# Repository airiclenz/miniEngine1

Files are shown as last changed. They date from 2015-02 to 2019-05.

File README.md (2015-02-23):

# miniEngine1
An Arduino based single-axis motion-control system for time-lapse photography (the legacy version)

This repository contains all that is needed to build a full miniEngine 1 system. It contains:

	- Software
	- Hardware (PCB CAD files)
	- Documentation
	- Licenses
	
The PCBs and most of the needed parts can be purchased here: http://shop.airiclenz.com  

Notice regarding compilation
----------------------------

The legacy code does not compile with the newest Arduino SDK! Please download the Arduino SDK version 1.0.6 from here: 

http://arduino.cc/en/Main/OldSoftwareReleases

This should compile the code just fine. You will also need to install the RTC library for being able to compile and upload the sketch. Details how to do that can be found in the documentation folder of this repository.

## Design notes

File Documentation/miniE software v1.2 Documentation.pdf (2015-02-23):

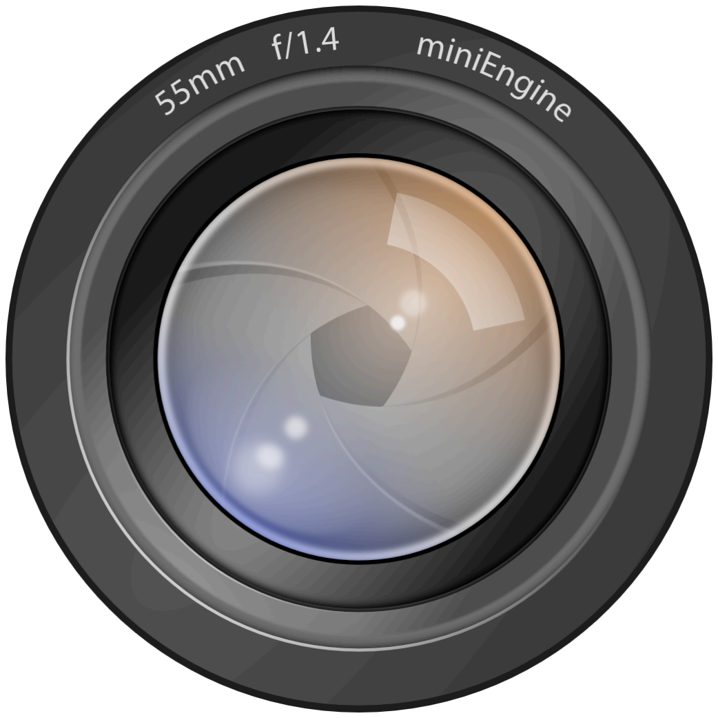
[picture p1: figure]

# miniE

### miniEngine - an open-source motion control system for timelapse photography

# Documentation of version 1.2

## Airic Lenz

### Content

| 1 | Introduction | 1
| 2 | Needed hardware | 1
| 3 | Installation | 3
| 4 | User interface and navigation | 4
| 5 | The Cycle | 5
| 6 | Functionalities | 6
| 6.1 | The main screen | 6
| 6.2 | Camera Functionalities / Settings | 7
| Cycle length | 7
| Focus time | 7
| Exposure time | 7
| Focus-line behaviour | 8
| Max shots | 8
| Post delay | 8
| Test shot | 8
| 6.3 | Motor Functionalities / Settings | 9
| Motor steps | 9
| Motor direction | 9
| Motor post delay | 9
| Move to home | 9
| Set motor home | 9
| Motor sleep | 9
| Max steps | 10
| Motor ramp | 10
| Max speed delay | 10
| Min speed delay | 10
| 6.4 | Programs | 11
| Add program | 11
| Program start time | 11
| Program weekdays | 12
| Program duration | 12
| Move motor home after program | 12
| Program status | 12
| Delete program | 12
| 6.5 | General settings | 13
| Operation mode | 13
Documentation | v1.2

| System time | 13
| Backlight delay | 13
| Backlight power | 13
| Limit switches | 13
| 6.6 | Settings | 14
| Save settings | 14
| Autosave settings | 14
| Reset settings | 14
| 6.7 | Version info | 14
Appendix | 15
Software License | 18
Hardware License | 18

### | 1 | Introduction

miniE is an engine sketch to provide control over a single stepper motor and camera, using an Arduino board and a DFRobot LCD Keypad shield. It is a minimalist design providing all the necessary features to do shoot-move-shoot or continuous timelapse with a built-in user interface. It was developed to provide a slim and easy way to timelapse photography. The first version of miniE was inspired by the OpenMoCo timelapse engine. For more details please have a look at www.airiclenz.com.

### | 2 | Needed hardware

For running the miniEngine you will need an Arduino Uno Board and the DFRobot Display shield for a minimal setup. With these components (and some breadboard magic) you are able to use the system as an intervalometer for your camera. To avoid the open wires and the breadboard I suggest the usage of a Arduino proto-shield for placing the electronics.

For a full setup that uses all capabilities of the current version, you will need the following components:

1x Arduino Uno

1x DFRobot Display Shield

1x RTC module (only needed for timed programs)

1x Stepper motor driver (e.g. EasyDriver)

1x Stepper motor fitting your requirements

1x Dolly system to control

Computer running Windows, Linux, or OSX compatible with the Arduino IDE (≥ 1.0)

Some additional material for wiring up all components (e.g. proto Shield, wires, …)

1x Camera remote cable (u can use a cheap remote for you camera model to get one)

You will also need some electric parts for setting up the required connections to all the external components (like camera, motor driver, ...). Here is a list of all parts needed (for more details have a look at the circuit diagram in the APPENDIX of this document):

CAM | 2.5 mm headphone jack (DigiKey PartNo.: CP1-2503A-ND)
LIMIT-SWITCHES | 2.5 mm headphone jack (DigiKey PartNo.: CP1-2503A-ND)
RTC | Sparkfun RTC MODULE (OPTIONAL)
MOTOR-CONTROL | Terminal screw block 1×3 (pitch 2.54 mm)
MOTOR-ENERGY | Terminal screw block 1×2 (pitch 2.54 mm)
OK1 | 4N35 Optocoupler (DIL-6)
OK2 | 4N35 Optocoupler (DIL-6)
R1 | 470 Ω Resistor (0207/10)
R2 | 470 Ω Resistor (0207/10)
R3 | 20 kΩ Resistor (0207/10)
R4 | 20 kΩ Resistor (0207/10)
R5 | 20 kΩ Resistor (0207/10; OPTIONAL)
S-DY1 | 12V 0.2A diode (e.g. fast zener or schottky diode); This part is OPTIONAL and by default bridged on the miniE shield
S-DY2 | 12V 0.2A diode (e.g. fast zener or schottky diode); This part is OPTIONAL and by default bridged on the miniE shield

If you plan to do timelapse photography from a tripod without any movement of the camera, you will of course not need the movement components like stepper motor, driver board or the dolly system.

### | 3 | Installation

If you don‘t already have installed the Arduino Development Suite, please download it from

http://arduino.cc

and install it. The miniE software can be downloaded from the OpenMoCo SourceForge subVersion repository:

http://openmoco.svn.sourceforge.net/viewvc/openmoco/miniE/trunk/miniE

Now, after you downloaded the project, please unzip (if you downloaded a tarBall) or copy it to any location you want. To successfully compile the miniE code, you need an external library, that is used within miniE. To be able to install the external library, please download it from:

https://github.com/jcw/rtclib

After you downloaded the library, you need to install it. To do so, unzip it. It should be in a folder of its own. Open the Arduino folder. This folder should be placed in your user accounts documents folder (You can check the path in the Arduino settings). On a Mac this folder usually can be found here:

/Users/USERNAME/Documents/Arduino

On a Windows system this folder should be placed here:

Drive:\Users\USERNAME\My Documents\Arduino

If there is already a folder there called libraries, place the RTClib folder in there. If not, create a folder called libraries in the Arduino folder, and drop the RTClib folder in there. Then re-start the Arduino programming environment.

Open the project by double clicking the main project file miniE.ino (all needed files will be loaded automatically then). For uploading the software to your Arduino board, connect your Arduino board (for details about connecting the Arduino, please check the Arduino website and the Arduino documentation) to your computer. Now press the upload button:

After the code was uploaded successfully, your Arduino board is ready for doing timelapse photography for you.

If you don‘t see anything on your screen, please adjust the LCD contrast.

### | 4 | User interface and navigation

The miniE user interface is based on a 2x16 char LCD display and 5 buttons. The full system control is available through this interface. Due to the limited space, available on such a LCD display, the full amount of data and settings is spread over different single setting screens which are available by navigating through a menu tree.

The navigation is based on the general principle that you move sideways through the user interface. A RIGHT key press brings you deeper into the menu structure while a LEFT key press brings you back up. The UP and DOWN keys are used for moving up and down on a menu- or information screen and for changing settings (toggle, increment, decrement). The complete menu tree can be found in Appendix 1 at the end of this document.

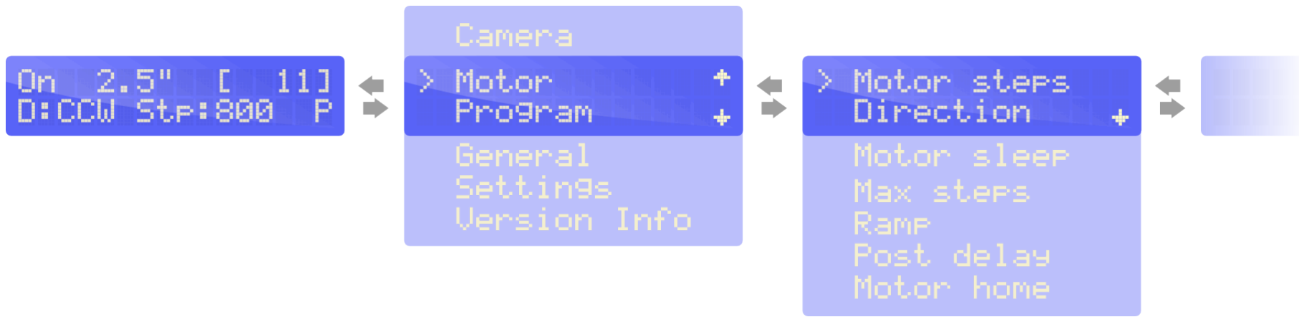
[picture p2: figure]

The navigation principle

### | 5 | The Cycle

The way miniE works can be described as a cycle. Please keep in mind that the total cycle length, you can define, is not a limiting factor. If "Focus time", "Exposure time", "Exposure post delay", the time the motor needs for the movement and the "Motor post delay" are in total longer than the cycle, all these steps will be performed fully in any case. If this happens, the "real“ cycle length is longer than the time you defined for it and equals the sum of all cycle steps.

The picture below shows the ideal situation where all the single steps take in total less time than the defined cycle length.

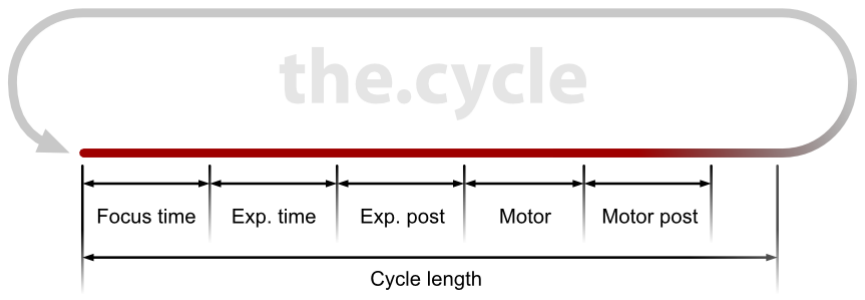
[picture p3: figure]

The cycle of miniE

### | 6 | Functionalities

| 6.1 | The main screen

The main screen is the control central of the miniE system. Here you can start and stop the engine, follow the process and view the most important settings and values. You start and stop the program by pressing the SELECT key.

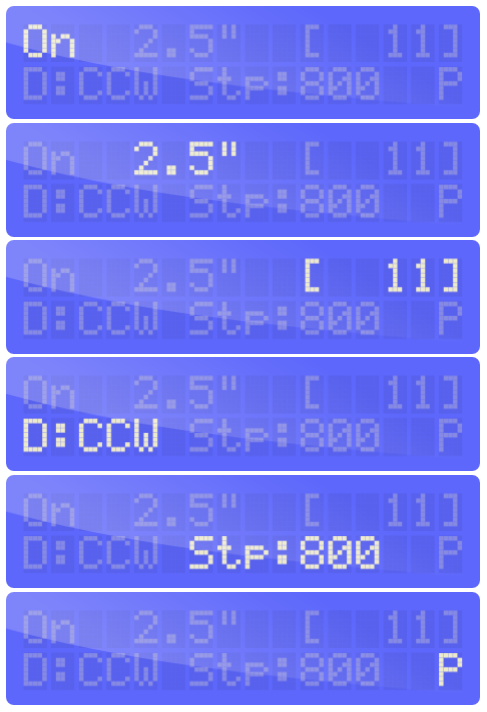
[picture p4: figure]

Status of the engine. This shows if the engine is running or stopped. You can start / stop it by pressing the SELECT key or through a program

Length of the full cycle. You can change this value under [Camera] - [Cycle length]

Number of shots taken since the engine start. This value will be reset every time the engine re-starts

Direction of the motor. CW = clockwise; CCW = counter/anti-clockwise; This can be changed under [Motor] - [Direction]

The number of steps to do during one cycle. This value can be changed under [Motor] -[Motor steps]

Program status. You can only see something here if at least one future program is programmed. If the engine is stopped, you see a static „P“. If you started the engine manually, you will see a blinking „!“ because you possibly prevent a timed program from running. If a timed program is running you will see a blinking „P“

| 6.2 | Camera Functionalities / Settings

| Cycle length

The cycle length defines the length of the main loop of the engine. A cycle length of 5 seconds means that the engine will take a photo every 5 seconds. After that all other cycle tasks, like motor movement, will be performed. After that the engine will wait until the 5 seconds are over (counted from the start of the cycle) and start a new cycle then.

| Focus time

The focus time is the first task during a cycle. It will trigger the focus line of the camera for the amount of milliseconds you defined. This can be used for focussing or to wake up the camera in very long cycles. If you set the focus time to zero, this task will not be performed.

| Exposure time

The exposure time is executed directly after focussing. It will trigger the exposure line of the camera for the amount of milliseconds you defined. This is actually triggering the shutter and doing the shot. You can use this to trigger your camera to do a shot in manual mode. In this case you have to set up your camera with your preferred manual settings.

For triggering the shutter, a minimal exposure time of about 40 milliseconds (1/25) is needed. This value changes from camera brand to camera brand.

If you want to do HDR shoots, you have to set up you camera to do all needed shots after one trigger signal. Another solution would be to expose as long as your camera needs to doo all HDR shots (set the camera drive to multi shot mode for this).

| Focus-line behaviour

This is setting the behaviour of the focus line during the exposure. You can choose between „high with shutter“ and „low with shutter“. This option is needed due to the fact that different camera brands need different signal combinations to accept the shutter signal.

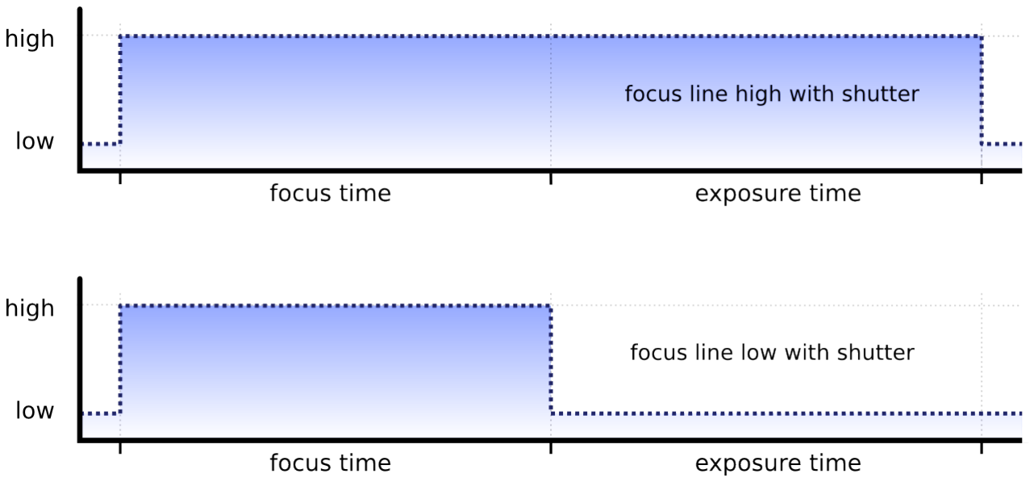
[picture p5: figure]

Focus line behaviour

| Max shots

This is defining a stop limit for the engine. After reaching this amount of shots, the engine will be stopped automatically. A value of „0“ means that there is no limit.

| Post delay

The post delay is a delay time after the exposure time is over. This can be used to ensure the camera has enough time to finnish the exposure before the motor starts to move.

| Test shot

Here you can check if your camera is connected properly and the settings are OK for your specific camera brand. This will do one single exposure with the duration of 1/10th of a second (100 milliseconds).

| 6.3 | Motor Functionalities / Settings

| Motor steps

This setting is for defining the amount of steps to do during your motor phase of the cycle. 1,600 steps are exactly one revelation with most of the stepper motors.

| Motor direction

Here you can set the direction of you motor. You can choose between clockwise and counter-clockwise.

| Motor post delay

This delay is usually used to let the dolly settle down after motor movement to avoid vibrations.

| Motor home menu

This menu contains all settings and functionalities for controlling the motor home behaviour. The motor home position is a free choosable position of the motor. The engine counts every step away from this position while the engine is running (started manually or by a program). You can move the motor back to its home position manually or automatically after a timed program finished.

The motor home position is cleared when miniE is powered up. This means that your motor always starts from home after miniE was powered up.

| Move to home

With this functionality you can move the motor back to its home position manually.

| Set motor home

This sets the current position of the motor as home position.

| Motor sleep

Motor sleep defines the behaviour of the driver board when the motor is not moved. This setting is only valid for the time when the engine is running. While the engine is stopped, the motor is always in sleep mode.

If your motor is in sleep mode between the movements, its energy consumption is drastically reduced.

You can turn sleep mode off to keep the motor powered as long as the engine is running. This is useful if you want to avoid any movements of your dolly during the run.

| Max steps

This is defining a stop limit for the engine. After reaching this amount of steps, the engine will be stopped automatically. A value of „0“ means that there is no limit.

| Motor ramp

This value is defining the amount of steps your motor will accelerate and decelerate through a motor movement phase.

If you defined a value of 200 steps for ramping and you are doing 1000 steps each cycle, your motor phase looks like this:

- 200 steps acceleration
- 600 steps max speed
- 200 steps deceleration

The motor ramping softly shaped for smooth movements.

| Max speed delay

This value defines the time between every motor step at maximum speed. The shorter the delay is, the faster your motor is running.

| Min speed delay

This value defines the time between every motor step at minimum speed (At the very beginning and at the very end of every motor phase). The longer the delay is, the slower your motor is running.

| 6.4 | Programs

Programs are used to start the engine automatically at a defined time and date. Programs only work if you have a Real-Time-Clock connected to your Arduino. You can define two types of programs:

- single date program - is only started once
- repeating weekday program - is started at the defined weekdays (e.g. every Monday)

You can define 30 programs. A programs is not started while you are editing it!

In the program list

In the graphic obove you can see the two different program types with their corresponding representation in the program list (24h time format):

- 10. Nov 0900 - Single date program - this program will only be started once (at the 10th November at 09:00 o‘clock in the morning, the year is not displayed in the program list)
- M_W_F_S 1700 - Repeating weekday program - this program is started every Monday, Wednesday, Friday and Sunday at 17:00 o‘clock. A program becomes automatically a repeating weekday program if at least one day of the week is activated for the program (see „Program weekdays“)

| Add program

You can add a new program with this functionality. After you added a program, you are automatically editing it.

| Program start time

You can edit the program start time here. This is the time the engine will started automatically. If the program is a single date program, you will be able to define a date (this is not the case if you are editing a repeating weekday program).

| Program weekdays

Here you can set weekdays at which you want the program to be started. If you deactivate all weekdays, the program becomes a single date program and will only be started once.

| Program duration

This value defines the duration in minutes the engine will be active after it was started by the program.

| Move motor home after program

If enabled, the motor will automatically move back to its home position (see Motor home for more information) after the program was stopped. The motor will be moved back on any event that stops the program (regular end, limit switch, manually stopped by the user).

| Program status

If enabled, the program is active and will be considerated by the internal timer. If you disable a program, it has the same effect as if it were not existing.

| Delete program

Here you can delete the program you are currently editing.

| 6.5 | General settings

| Operation mode

The operation mode is defining the basic way the miniEngine will work. You can choose between two different modes:

- shoot-move-shoot mode - the shoot-move-shoot mode is doing all steps of the cycle sequentially. This means the camera is triggered, then the motor moves, and then the cycle begins again.
- continuous mode - in this mode the motor is moving continually (The amount of defined steps per cycle). The camera is triggered while the motor is moving.

| System time

You can set the system time here. This functionality is only available if you have a Real-Time-Clock connected to your system.

| Backlight delay

This value defines the time in seconds the system is waiting after the last user action, until shutting off the LCD-backlight.

| Backlight power

Here you can set the brightness of your LCD-backlight.

| Limit switches

You can turn the limit-switches on or off. If you disable your limit switches, a triggered limit-switch will not stop the running engine.

This functionality is included because a not installed limit switch can cause unwanted limit switch events (the Arduino ports, used for the limit switches, are very sensitive and need to be pulled down to ground through a pull-down resistor with a value between 1kΩ and 50kΩ). If there is no pull-down resistor, it is better to turn off the limit switches.

| 6.6 | Settings

| Save settings

This functionality is saving all your defined values and settings to the internal EEPROM of the Arduino board. After powering the system all settings and values are automatically loaded from the EEPROM.

| Autosave settings

You can save all settings and values automatically. If you enable this functionality the the settings are automatically saved after you changed any setting or value and left the corresponding setting / value screen.

| Reset settings

This functionality is resetting all settings and values to the default values. It is also deleting all defined programs.

| 6.7 | Version info

Some information about the current installed version of miniEngine.

### Appendix

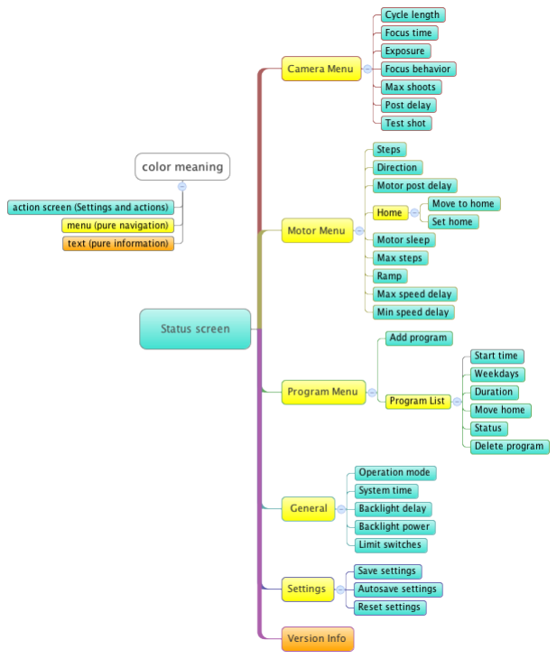
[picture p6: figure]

APPENDIX 1 - The menu tree

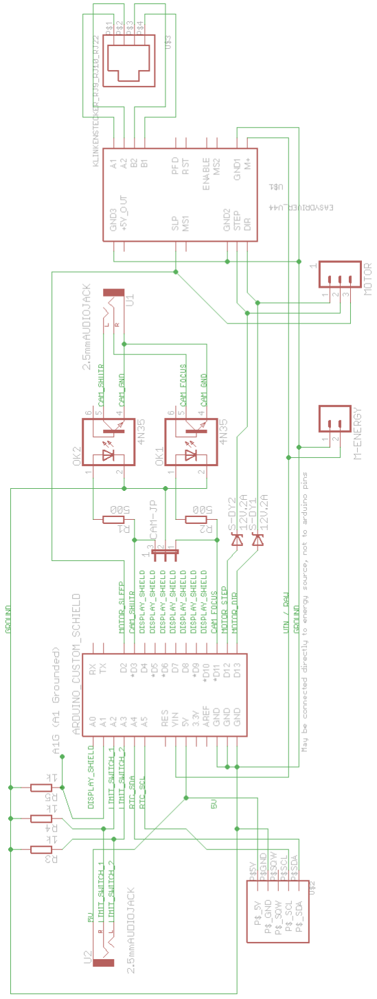
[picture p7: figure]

APPENDIX 2 - Circuit diagram

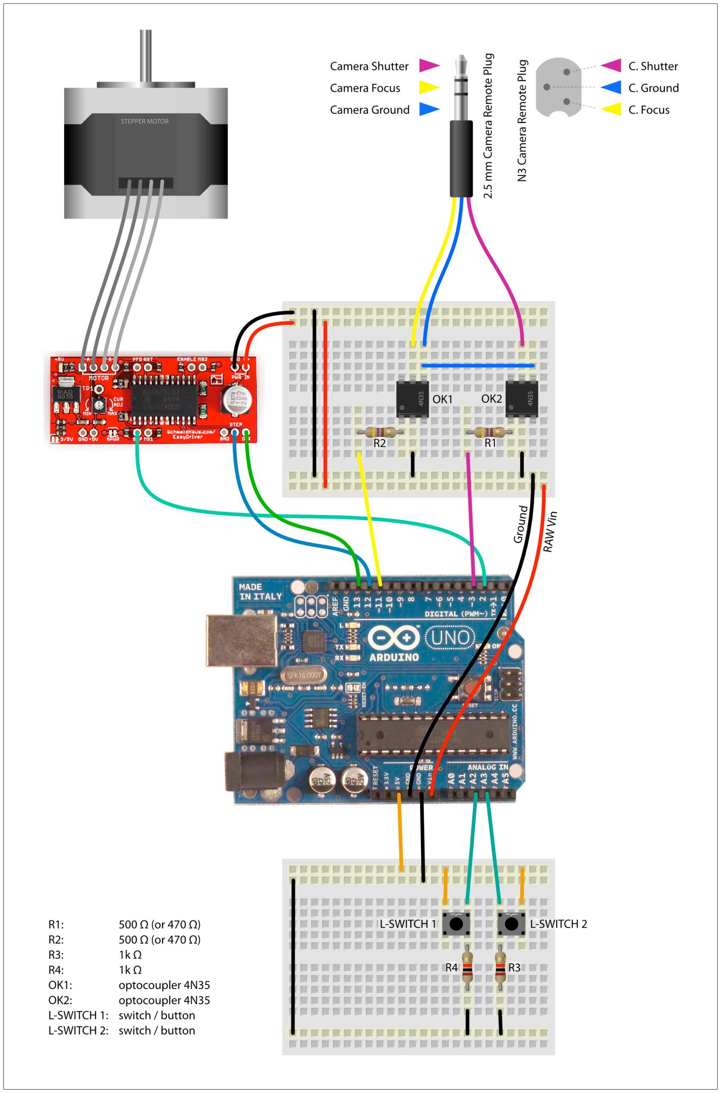
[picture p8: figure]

APPENDIX 3 - Arduino breadboard circuit

### Software License

The miniEngine software is free software: you can redistribute it and/or modify it under the terms of the GNU General Public License as published by the Free Software Foundation, either version 3 of the License, or (at your option) any later version.

The miniEngine software and all belonging material is distributed in the hope that it will be useful, but WITHOUT ANY WARRANTY; without even the implied warranty of MERCHANTABILITY or FITNESS FOR A PARTICULAR PURPOSE. See the GNU General Public License for more details.

You should have received a copy of the GNU General Public License along with this program. If not, see http://www.gnu.org/licenses/.

### Hardware License

All hardware designs and schematics provides along with the miniE software are free. You can redistribute it and/or modify it under the terms of the CERN Open Hardware Licence 1.1, or (at your option) any later version.

The hardware documentation and hardware files are distributed in the hope that they will be useful, but WITHOUT ANY WARRANTY; without even the implied warranty of MERCHANTABILITY or FITNESS FOR A PARTICULAR PURPOSE. See the CERN Open Hardware Licence for more details.

You should have received a copy of the CERN Open Hardware Licence along with these files. If not, see http://www.ohwr.org/projects/cernohl/wiki/.

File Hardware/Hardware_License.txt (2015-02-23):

CERN OPEN HARDWARE LICENCE v1.1

Preamble

Through this CERN Open Hardware Licence ("CERN OHL") version 1.1, the
Organization wishes to disseminate its hardware designs (as published
on http://www.ohwr.org/) as widely as possible, and generally to
foster collaboration among public research hardware designers. The
CERN OHL is copyright of CERN. Anyone is welcome to use the CERN OHL,
in unmodified form only, for the distribution of his own Open Hardware
designs. Any other right is reserved.  

1. Definitions

In this Licence, the following terms have the following meanings:

“Licence” means this CERN OHL.  

“Documentation” means schematic diagrams, designs, circuit or circuit
board layouts, mechanical drawings, flow charts and descriptive text,
and other explanatory material that is explicitly stated as being made
available under the conditions of this Licence. The Documentation may
be in any medium, including but not limited to computer files and
representations on paper, film, or any other media.  

“Product” means either an entire, or any part of a, device built using
the Documentation or the modified Documentation.  

“Licensee” means any natural or legal person exercising rights under
this Licence.  

“Licensor” means any natural or legal person that creates or modifies
Documentation and subsequently communicates to the public and/ or
distributes the resulting Documentation under the terms and conditions
of this Licence.  

A Licensee may at the same time be a Licensor, and vice versa.

2. Applicability

2.1 This Licence governs the use, copying, modification, communication
to the public and distribution of the Documentation, and the
manufacture and distribution of Products. By exercising any right
granted under this Licence, the Licensee irrevocably accepts these
terms and conditions.  

2.2 This Licence is granted by the Licensor directly to the Licensee,
and shall apply worldwide and without limitation in time. The Licensee
may assign his licence rights or grant sub-licences.  

2.3 This Licence does not apply to software, firmware, or code loaded
into programmable devices which may be used in conjunction with the
Documentation, the modified Documentation or with Products. The use of
such software, firmware, or code is subject to the applicable licence
terms and conditions.  

3. Copying, modification, communication to the public and distribution
of the Documentation

3.1 The Licensee shall keep intact all copyright and trademarks
notices and all notices that refer to this Licence and to the
disclaimer of warranties that is included in the Documentation. He
shall include a copy thereof in every copy of the Documentation or, as
the case may be, modified Documentation, that he communicates to the
public or distributes.

3.2 The Licensee may use, copy, communicate to the public and
distribute verbatim copies of the Documentation, in any medium,
subject to the requirements specified in section 3.1.

3.3 The Licensee may modify the Documentation or any portion
thereof. The Licensee may communicate to the public and distribute the
modified Documentation (thereby in addition to being a Licensee also
becoming a Licensor), always provided that he shall: 
a. comply with section 3.1;
b. cause the modified Documentation to carry prominent notices stating
that the Licensee has modified the Documentation, with the date and
details of the modifications;
c. license the modified Documentation under the terms and conditions
of this Licence or, where applicable, a later version of this Licence
as may be issued by CERN; and
d. send a copy of the modified Documentation to all Licensors that
contributed to the parts of the Documentation that were modified, as
well as to any other Licensor who has requested to receive a copy of
the modified Documentation and has provided a means of contact with
the Documentation.

3.4 The Licence includes a licence to those patents or registered
designs that are held by the Licensor, to the extent necessary to make
use of the rights granted under this Licence. The scope of this
section 3.4 shall be strictly limited to the parts of the
Documentation or modified Documentation created by the Licensor.

4. Manufacture and distribution of Products

4.1 The Licensee may manufacture or distribute Products always
provided that the Licensee distributes to each recipient of such
Products a copy of the Documentation or modified Documentation, as
applicable, and complies with section 3.

4.2 The Licensee is invited to inform in writing any Licensor who has
indicated its wish to receive this information about the type,
quantity and dates of production of Products the Licensee has (had)
manufactured.

5. Warranty and liability

5.1 DISCLAIMER – The Documentation and any modified Documentation are
provided "as is" and any express or implied warranties, including, but
not limited to, implied warranties of merchantability, of satisfactory
quality, and fitness for a particular purpose or use are disclaimed in
respect of the Documentation, the modified Documentation or any
Product. The Licensor makes no representation that the Documentation,
modified Documentation, or any Product, does or will not infringe any
patent, copyright, trade secret or other proprietary right. The entire
risk as to the use, quality, and performance of a Product shall be
with the Licensee and not the Licensor. This disclaimer of warranty is
an essential part of this Licence and a condition for the grant of any
rights granted under this Licence. The Licensee warrants that it does
not act in a consumer capacity.

5.2 LIMITATION OF LIABILITY – The Licensor shall have no liability for
direct, indirect, special, incidental, consequential, exemplary,
punitive or other damages of any character including, without
limitation, procurement of substitute goods or services, loss of use,
data or profits, or business interruption, however caused and on any
theory of contract, warranty, tort (including negligence), product
liability or otherwise, arising in any way in relation to the
Documentation, modified Documentation and/or the use, manufacture or
distribution of a Product, even if advised of the possibility of such
damages, and the Licensee shall hold the Licensor(s) free and harmless
from any liability, costs, damages, fees and expenses, including
claims by third parties, in relation to such use.

6. General

6.1 The rights granted under this Licence do not imply or represent
any transfer or assignment of intellectual property rights to the
Licensee.

6.2 The Licensee shall not use or make reference to any of the names,
acronyms, images or logos under which the Licensor is known, save in
so far as required to comply with section 3. Any such permitted use or
reference shall be factual and shall in no event suggest any kind of
endorsement by the Licensor or its personnel of the modified
Documentation or any Product, or any kind of implication by the
Licensor or its personnel in the preparation of the modified
Documentation or Product.

6.3 CERN may publish updated versions of this Licence which retain the
same general provisions as this version, but differ in detail so far
this is required and reasonable. New versions will be published with a
unique version number.

6.4 This Licence shall terminate with immediate effect, upon written
notice and without involvement of a court if the Licensee fails to
comply with any of its terms and conditions, or if the Licensee
initiates legal action against Licensor in relation to this
Licence. Section 5 shall continue to apply.

6.5 Except as may be otherwise agreed with the Intergovernmental
Organization, any dispute with respect to this Licence involving an
Intergovernmental Organization shall, by virtue of the latter's
Intergovernmental status, be settled by international arbitration. The
arbitration proceedings shall be held at the place where the
Intergovernmental Organization has its seat. The arbitral award shall
be final and binding upon the parties, who hereby expressly agree to
renounce any form of appeal or revision.

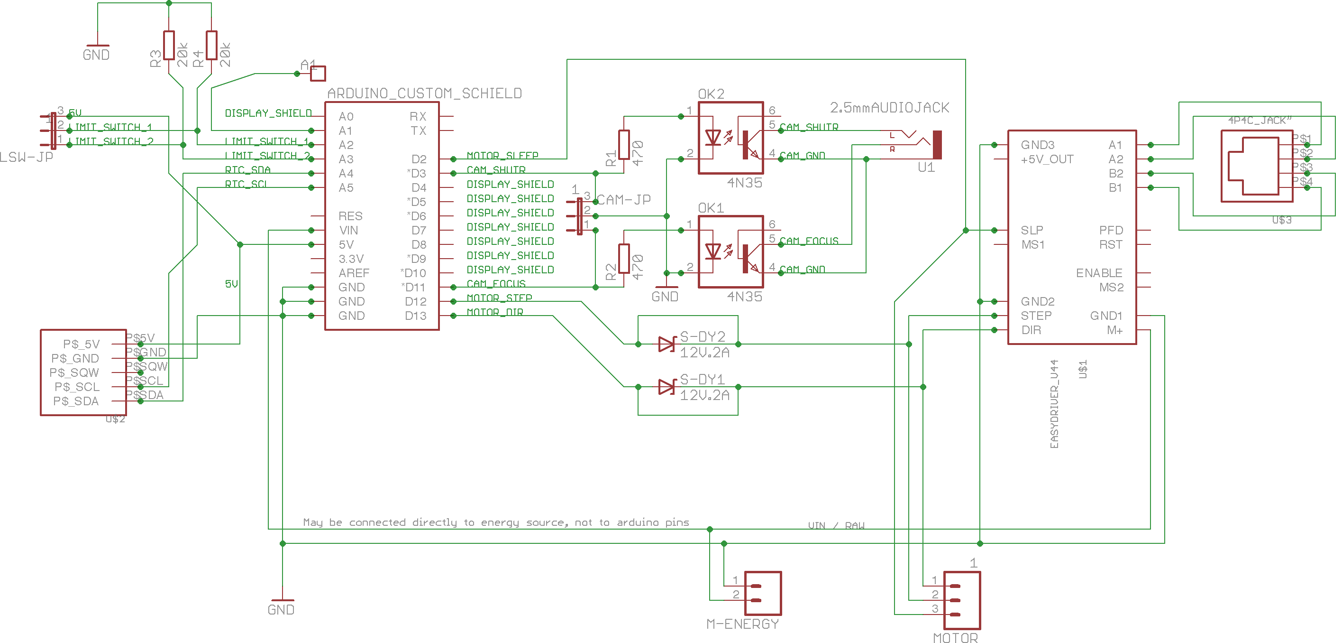
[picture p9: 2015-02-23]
Hardware/miniE_arduino_shield_v1-3.png

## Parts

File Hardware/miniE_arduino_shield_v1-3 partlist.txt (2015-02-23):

miniE shield - version 1.2 - part list
2012 by Airic Lenz

===================================================================================
PART                   VALUE / TYPE           PACKAGE                 
===================================================================================
CAM                    2.5MM HEADPHONE JACK   DigiKey PartNo.: CP1-2503A-ND                   
LSW	                   TERMINAL               Terminal-1x3 (2.54mm pitch)       
OK1                    4N35                   DIL06 OPTOCOUPLER                     
OK2                    4N35                   DIL06 OPTOCOUPLER                     
R1                     470~510 Ohm            RESISTOR 0207/10                     
R2                     470~510 Ohm            RESISTOR 0207/10                    
R3                     10k~20k Ohm            RESISTOR 0207/10                     
R4                     10k~20k Ohm            RESISTOR 0207/10                     
EASYDRIVER v4.4        -                      EASYDRIVER V4.4              
MOTOR                  4C4C PHONE JACK        DigiKey PartNo.: AE10381-ND	

OPTIONAL:
===================================================================================
PART                   VALUE / TYPE           PACKAGE                 
===================================================================================

S-DY1                  12V 0.2A               DIODE schottky/zener (bridged by default)            
S-DY2                  12V 0.2A               DIODE schottky/zener (bridged by default)        

If no EasyDriver should be used:
-----------------------------------------------------------------------------------
( MOTOR ) CONTROL      TERMINAL               Terminal-1x3 (2.54mm pitch)		
( MOTOR ) POWER        TERMINAL               Terminal-1x2 (2.54mm pitch)                        

If the camera should be triggered via infrared-LED:
-----------------------------------------------------------------------------------
IR                     TERMINAL               Terminal-1X3 (2.54mm pitch)

If you want to use scheduled programs:
(see http://www.sparkfun.com/products/99 for the used module)
-----------------------------------------------------------------------------------
RTC MODULE             DS1307                 SPARKFUN RTC MODULE (BOB-00099)

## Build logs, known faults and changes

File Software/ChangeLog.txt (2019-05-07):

===============================================================================
   C H A N G E   L O G  -   m i n i E n g i n e
===============================================================================

=====  v1.2a  ===  2019-05-07  ================================================

-	Adaption to the latest Arduinio SDK version

=====  v1.2  ===  2015-02-23  =================================================

-	bug fixes
-	Improved the motor min-speed code

=====  v1.1  ===  2012-05-06  =================================================

-	added 2 new ramping types -> now 3 motor ramping types
	(which is bes used can be changed in the code)
	main file line 133)
	> ARCTAN (new default - much smoother)
	> LINEAR
	> SINUS
- 	added limit switch checks to the motor phases (every 150ms)
-	added check for SELECT key to the motor phases (motor phases are no longer
	blocking)

=====  v1.00 ===  2012-03-22  =================================================

-	fixed a bug with minimum values (backlight time = zero problem)

=====  v0.12 ===  2012-02-13  =================================================

-	fixed a bug in the menu navigation
-	fixed a bug that if on system-time-screen the time is now updated
	automatically
- 	changed the ramping algorithm - ramping is now much smoother

=====  v0.11 ===  2012-02-12  =================================================

-	fixed a bug in the menu navigation - in some cases one were
	not able to move away from the main status screen
-	optimized key values (analogue values) for more precise key readings

=====  v0.10 ===  2012-01-06  =================================================

-	Upgraded MiniE to be compatible with Arduino 1.0
-	Fixed link to new Arduino 1.0 jeelabs RTC Lib
- 	Extended limit switch slightly where it will reverse the motor and
  	run one load of steps in the reverse direction to stop limit switch
- 	Lowered the detection for the limit switches (from 1023 to more than 1000)
- 	Reduced strings used to lower sketch size, Arduino 1.0 ended up blowing
  	the size out by 200bytes, pushign it over the UNO & ATMega328p limit
- 	Created new function to fill out menus to reduce code size (Could still be
  	extended to include other menus)

=====  v0.9 ===  2011-10-09  ==================================================

-	Added documentation for v0.9

=====  v0.9 ===  2011-09-21  ==================================================

-	Added units to the different setting-screens
-	Menu positions are now saved. When you go back in a menu, the focus is
	placed on the item you were at before
-	Added two 1k resistors to the two limit switch pins to generate clear
	signals (see circuit diagram for more details) and avoid unwanted
	limit-switch-triggerings
-	Added the possibility to enable/disable limit switches in the software
-	Added the possibility to set min and max motor speeds (step delays:
	big delay = slow; short delay = fast)
-  	Fixed the issue that focus line did not close after program end and
	during motor home movement

=====  v0.8.1 ===  2011-09-14  ================================================

-	Minor bugfix (system time editor)

=====  v0.8 ===  2011-09-13  ==================================================

-	The "P" for existing programs on the main screen is now only
	displayed if there are programs that will become active in the future.
	(smart "P")
-	Added a motor post delay
-	The system time is now editable
-	Updated copyright information
-	Fixed an issue that led the engine to heavy lagging while starting and
	stopping the continuous mode
-	Fixed a bug that crashed the engine in continuous mode after a limit
	switch event

=====  v0.7 ===  2011-09-07  ==================================================

-	Continuous mode is now 100% precise
-	Cycle length can now be adjusted in 0.5 second steps
-	Fixed a bug in motor-home counting
-	Fixed crashed motor ramping from version 0.6

=====  v0.6 ===  2011-09-06  ==================================================

-	Extensive optimisations of the UI code regarding RAM usage
-	Added RTC functionality
-	Added the possibility to create up to 30 programs
	(single date programs, repeating weekday programs)
-	Programs can be saved / autosaved together with the settings
-	Deleted "load settings" (useless because settings are automatically
	loaded during boot)
-	Added "reset settings" functionality. This resets all settings to
	factory default and deletes all programs.
-	Added message system to allow pop-up screen messages
-	Bugfix of a limit switch error that allowed one more cycle with triggered
	limit switch when restarting the engine
-	Minor bugfixes, code- and usability optimisations

=====  v0.5 ===  2011-08-29  ==================================================

-	Fixed the motor pin error (exchanged pin 12 & 13 to fit the circuit
	diagram)
-	added EEPROM functionality for saving and restoring all settings
-	Optimized menu code (in preparation for the RTC-program feature coming)
-	Added max shot limit
-	Added max motor step limit (counting from motor home)
-	Added backlight control features (duration and brightness)
- 	Minor bugfixes
-	Moved limit switch pins to analog pins 3 and 4

=====  v0.4 ===  2011-08-26  ==================================================

-	Minor code optimizations
-	Optimized long-key-press speed up
-	Added limiting switches check to analog pins 4 and 5.
	When connected to 5V the program stopps
-	Added the motor-home counter for the continuous mode - motor home now
	works in continuous mode too
-	The number of shoots done now stays displayed after the program stopped
-	Fixed an error in home counting in shoot-move-shoot mode

=====  v0.3  ===  2011-08-19  ==================================================

-	Changed the default value for focus line behavior to low with shutter
-	Implemented motor sleep functionality (new menu entry in "Motor")
	(motor is always in sleep while program stopped)
-	Added resistors in front of the optocouplers and updated the circuit
	diagram

=====  v0.2  ===  2011-08-18  ==================================================

-	Camera focus was implemented and is executed before the
	camera exposes (new menu entry under "Camera")
-	"Focus behavior" was implemented. This is setting the behavior
	of the focus line while exposing (high or low) (new menu
	entry in "Camera")
-	Added a little documentation describing "the cycle" of miniE

=====  v0.1  ===  2011-07-06  ==================================================

First version with the following features:

-	Arduino (ATMega) based Motion Control system
	for use with the DFRobot LCD Shield
-	System control is fully implemented as a 5 button -
	16x2 char GUI
-	Supports 1 stepper motor
-	Supports 1 camera
-	Shoot-move-shoot mode
-	continuous mode (needs to be improved)
-	Sinus shaped motor ramping (up to 32 mio steps)
-	Auto backlight-off after 15 seconds
	(still hard wired in the code)
- 	Motor home (for shoot-move-shoot mode)
-	Exposure post delay

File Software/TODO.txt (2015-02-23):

TODO

[ ] change limit switch behaviour from default low to default high if possible

[ ] Implement better limit-switch-event-protocol:
		1. Limit switch detected
		2. Pause for a moment (configurable?)
		3. Reverse at say 1/2 the forward speed (or the minimum speed) until the limit 
		   switch is released (i.e JUST far enough for the limit switch not to 
		   be operated). 

[ ] add #defines which are used to set the drivers specific motor awake or asleep states
	(e.g. sleep = high; awake = low)
	
[ ] add manual clear / auto clear behavior (of the shots taken)

[ ] it would be nice to use max steps and the cycle time to show a 
	calculation of the time to traverse the entire rail.	
	
[ ]	Jog function

[ ]	Add help screens "behind" the action screens describing
	the related function (only if there is flash memory left)
  		
[ ] Tidy up other menu LCD creation steps.

[ ] Move to end (till limit switch).

[ ] Fit IR trigger code in

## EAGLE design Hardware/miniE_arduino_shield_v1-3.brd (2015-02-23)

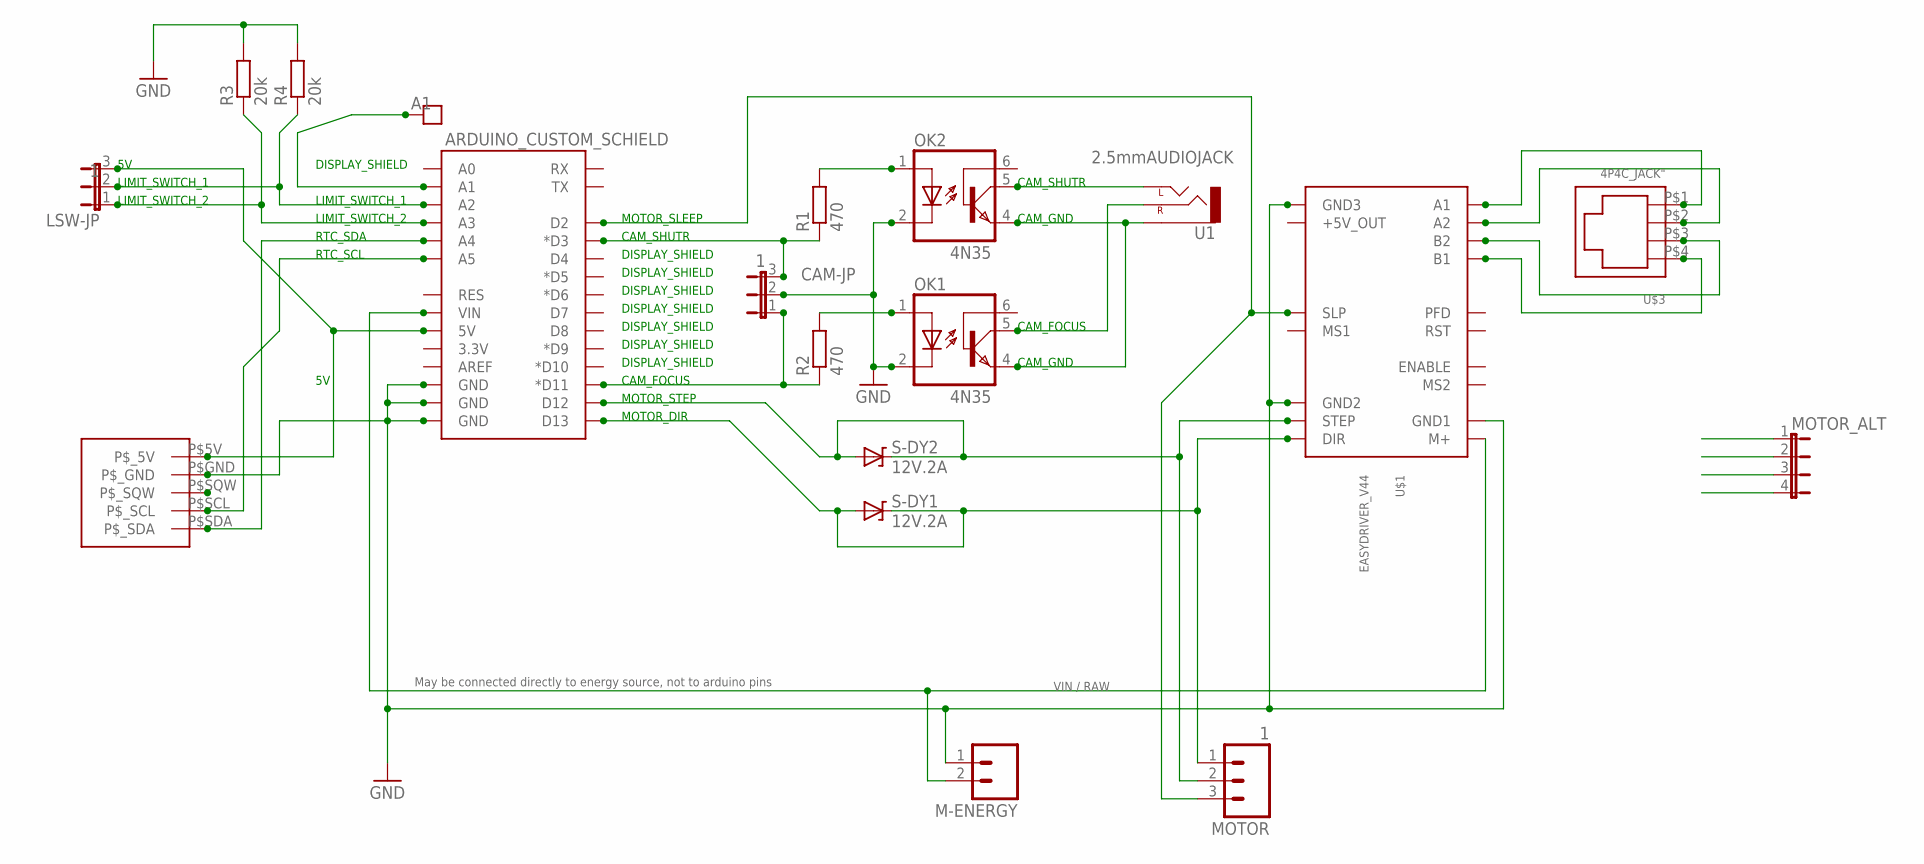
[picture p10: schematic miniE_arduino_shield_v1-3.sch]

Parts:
ARDUINO_CUSTOM_SCHIELD: ARDUINO_SHIELDNOLABELS; DUEMILANOVE_SHIELD_NOLABELS
CAM-JP: 1; JP2
LSW-JP: 1; JP2
M-ENERGY: MOLEX_02; 1X02
MOTOR: 1; 1X03
MOTOR_ALT: JP4E; JP4
OK1, OK2: 4N35; DIL06
R1, R2: 470; 0207/10
R3, R4: 20k; 0207/10
S-DY1, S-DY2: 12V.2A; DIODE-ZENER
U1: 2.5mmAUDIOJACK; STEREOJACK2.5MM_STEREOJACK2.5MM
U$1: EASYDRIVER_V44
U$2: SPARKFUN_RTC_MODULE-OPTIONAL; SPARKFUN_RTC_MODULE_OPTIONAL
U$3: 4P4C_JACK"; 4P4C_JACK-ASS-2004-3-4-LP-N-R
U$4: JUMPER_1X1

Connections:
+5V: ARDUINO_CUSTOM_SCHIELD.5V, LSW-JP.3, U$2.P$5V (P$_5V)
A1: MOTOR_ALT.1, U$1.A1, U$3.P$1
A2: MOTOR_ALT.2, U$1.A2, U$3.P$2
B1: MOTOR_ALT.4, U$1.B1, U$3.P$4
B2: MOTOR_ALT.3, U$1.B2, U$3.P$3
CAM_FOCUS: OK1.5 (COL), U1.RING1 (RIGHT), U1.RING2 (RIGHT)
CAM_GND: OK1.4 (EMI), OK2.4 (EMI), U1.SLEEVE
CAM_SHUTTER: OK2.5 (COL), U1.TIP (LEFT)
GND: ARDUINO_CUSTOM_SCHIELD.GND@0 (GND), ARDUINO_CUSTOM_SCHIELD.GND@1 (GND), ARDUINO_CUSTOM_SCHIELD.GND@2 (GND), CAM-JP.2, M-ENERGY.1, OK1.2 (C), OK2.2 (C), R3.2, R4.2, U$1.GND1, U$1.GND2, U$1.GND3, U$2.P$GND (P$_GND)
unnamed: ARDUINO_CUSTOM_SCHIELD.D12, MOTOR.2, S-DY2.P$1 (C), S-DY2.P$2 (A), U$1.STEP
unnamed: ARDUINO_CUSTOM_SCHIELD.D11 (*D11), CAM-JP.1, R2.1
unnamed: ARDUINO_CUSTOM_SCHIELD.D3 (*D3), CAM-JP.3, R1.1
unnamed: ARDUINO_CUSTOM_SCHIELD.D13, MOTOR.1, S-DY1.P$1 (C), S-DY1.P$2 (A), U$1.DIR
unnamed: ARDUINO_CUSTOM_SCHIELD.D2, MOTOR.3, U$1.SLEEP (SLP)
unnamed: OK2.1 (A), R1.2
unnamed: OK1.1 (A), R2.2
unnamed: ARDUINO_CUSTOM_SCHIELD.A2, LSW-JP.2, R4.1
unnamed: ARDUINO_CUSTOM_SCHIELD.A3, LSW-JP.1, R3.1
unnamed: ARDUINO_CUSTOM_SCHIELD.A4, U$2.P$SDA (P$_SDA)
unnamed: ARDUINO_CUSTOM_SCHIELD.A5, U$2.P$SCL (P$_SCL)
unnamed: ARDUINO_CUSTOM_SCHIELD.A1, U$4.P$1
VIN: ARDUINO_CUSTOM_SCHIELD.VIN, M-ENERGY.2, U$1.M+

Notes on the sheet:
CAM_FOCUS
CAM_GND
CAM_SHUTR
DISPLAY_SHIELD
MOTOR_SLEEP
MOTOR_STEP
MOTOR_DIR
LIMIT_SWITCH_1
LIMIT_SWITCH_2
RTC_SDA
RTC_SCL
VIN / RAW
May be connected directly to energy source, not to arduino pins

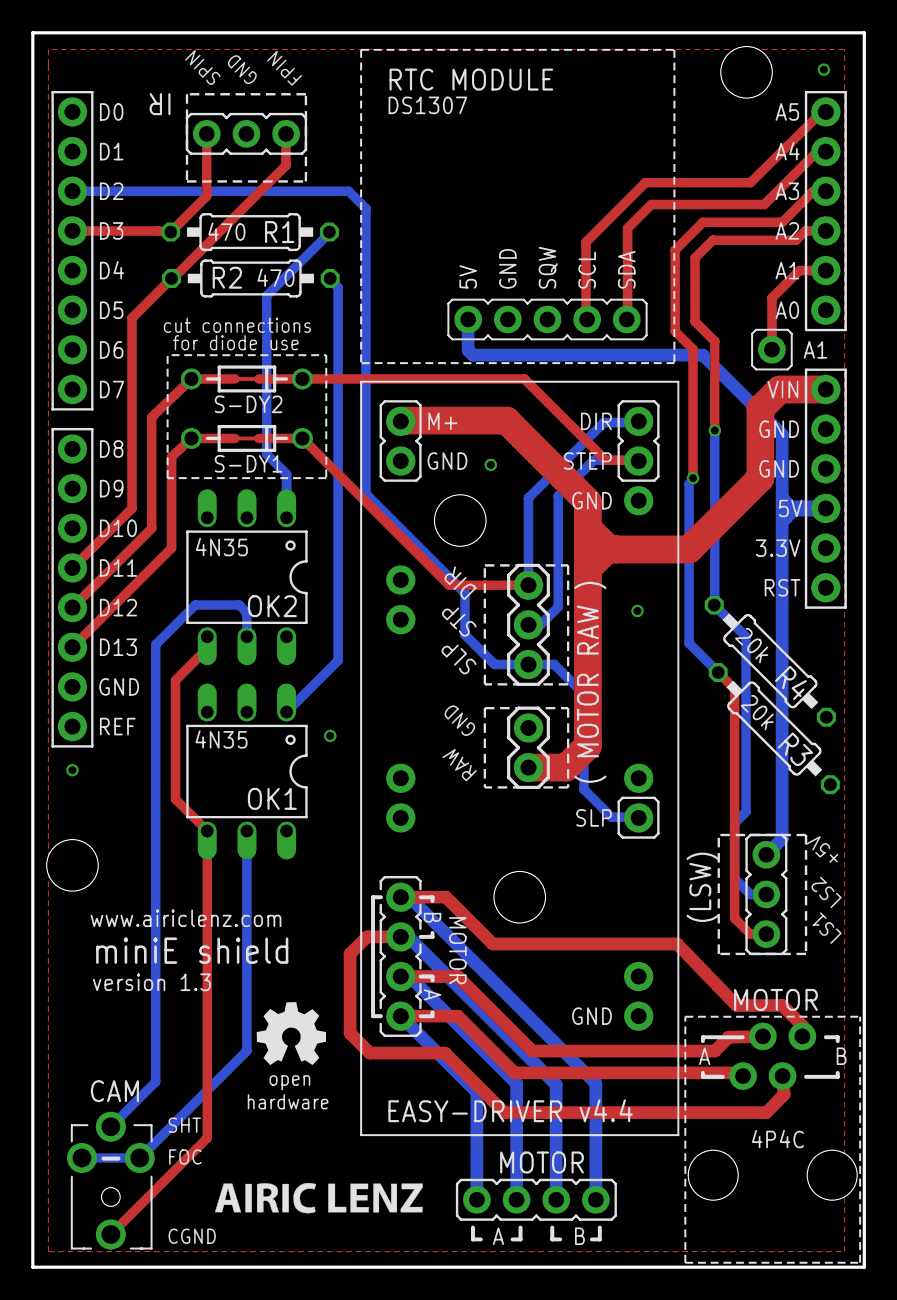
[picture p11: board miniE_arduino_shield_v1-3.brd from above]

Board: 4 copper layers, 53.3 x 79.1 mm, 19 parts (0 on the bottom side), 22 nets.

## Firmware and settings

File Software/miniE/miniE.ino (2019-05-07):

/*

    See www.openmoco.org for more information

    2015 Airic Lenz, C.A. Church

    The 1st version of this code, dealing with core functionalities,
    was heavily inspired by the OpenMoCo Engine by C.A. Church
    and is basically based on it. Thank you for your great work!

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
 */

// Max sketch size size for 32k Arduinos: 28,672 bytes = 0x7000


#include "Wire.h"
#include "LiquidCrystal.h"
#include "EEPROM.h"
#include <avr/pgmspace.h>
#include <RTClib.h>           // Install via "Tools --> Manage Libraries"
// #include <MemoryFree.h>    // See http://www.arduino.cc/playground/Code/AvailableMemory


// --------------------------
// Version of the software

#define VERSION             1
#define SUBVERSION          3


// --------------------------
// Arduino pins

// pin to tell the motor drivers to go to sleep
#define MOTOR_SLEEP_PIN     2
#define MOTOR_STEP_PIN      12
#define MOTOR_DIR_PIN       13

// shutter and focus connections
#define CAMERA_PIN          3
#define FOCUS_PIN           11

// pin for LCD backlight
#define LCD_BACKLIGHT_PIN   10
// pin for reaing analog key input
#define LCD_KEY_PIN         A0


// limit switches for stopping the program
// one for each side of teh dolly
#define LIMIT_SWITCH_PIN_1  A2
#define LIMIT_SWITCH_PIN_2  A3



// --------------------------
// General action status flags:
//
// B0 = operating mode (0 = shoot-move-shoot; 1 = continuous)
// B1 = camera focussing
// B2 = start cycle immediately
// B3 = camera shooting
// B4 = program running
// B5 = camera post exposure
// B6 = motor slot open
// B7 = motor post delay is active

byte action_status = B0;

// the time we started with an action (focussing, exposure, post delay)
unsigned long action_start_time;

// --------------------------
// Camera settings

// cycle length of the whole cycle in half seconds (4 * 0.5 = 2 seconds)
unsigned int cycle_length = 4;

// camera shoot counter
unsigned int camera_shoot_count     = 0;
// the focus line will be risen before the exposure is done (in milliseconds)
unsigned int camera_focus_time      = 0;
// the time we want to expose our pictures (in milliseconds)
unsigned int camera_exp_time        = 100;
// time after exposure before the motor is moved (in milliseconds)
unsigned int camera_exp_post        = 200;

// the maximum amount of shots to do (0 = unlimited)
unsigned int camera_shot_max        = 0;

// --------------------------
// defines the camera behaviour
//
// B0 = Focus line high or low while exposing
// B1 =
// B2 =
// B3 =
// B4 =
// B5 =
// B6 =
// B7 =


byte camera_status        = B0;



// --------------------------
// Motor settings



// motor ramping types
#define RAMPING_LINEAR        0
#define RAMPING_ATANGENS      1
#define RAMPING_SINUS         2


// used motor ramping
#define MOTOR_RAMP_TYPE       RAMPING_ATANGENS // see the definitions just before this line for possible choices.

// acceleration and decelleration time (in steps)
unsigned int motor_ramp            = 500;
// total number of pulses for move (1600 steps per rev)
unsigned long motor_steps           = 0;
// number of maximum steps the motor is allowed to do  (0 = unlimited)
unsigned long motor_steps_max       = 0; // 0 = no limit
// delay after motor movement
unsigned int motor_post             = 0;
// maximum delay in microsecond (delay between steps at minimum
// speed of the motor (start and endphase)).
unsigned long motor_step_delay_max   = 15000;
// minimum delay in microseconds (delay between steps at maximum speed of the motor)
unsigned long motor_step_delay_min   = 100;

// the amount of steps done away from the defined home position
// clockwise = direction bit low (positive count)
// anti-clockwise = direction bit high (negative count)
long home_steps                    = 0;



// General Motor status flags:
//
// B0 = sleep on / off (the pin has to be set inverse --> sleep on = pin low)
// B1 = limit switches on / off
// B2 =
// B3 =
// B4 = motor direction
// B5 =
// B6 =
// B7 =

byte motor_status  = B11000000;


// the time we started the program
unsigned long program_start_time;

// --------------------------
// Display
// initialize the library with the numbers of the interface pins
LiquidCrystal lcd(8, 9, 4, 5, 6, 7);



// --------------------------
// Timed-Programs (RTC) status flags:
//
// B0 = timed-program running
// B1 = active programs in the future
// B2 =
// B3 =
// B4 =
// B5 =
// B6 =
// B7 =

byte program_status = B0;

// the max number of programs available
#define program_amount    20

// the program that is curently edited, 255 = no program is editet
byte current_program =    255;

// the program that is curently running
byte running_program =    255;

// the number of programs we have defined;
byte program_count =      0;

// day flags of the programs
// B0  monday
// B1  tuesday
// B2  wednesday
// B3  thursday
// B4  friday
// B5  saturday
// B6  sunday
// B7  use weekdays (low = use single date)

byte program_weekdays[program_amount];

// start date and time of the program
DateTime program_datetime[program_amount];

// program duration in minutes
unsigned int program_duration[program_amount];

// other flags of the programs
//
// B0  enabled / disabled
// B1  move back to home
// B2
// B3
// B4
// B5
// B6
// B7

byte program_flag[program_amount];

// content of the menu (we initialize the array with some items -
// fitting the longest possible menu - have a look at mE_program
// to check the program amount!!! - all programs will be listed in
// one menu - the longest regular menu is 7 items long)
char lines[20][17];




// --------------------------
// User interface

// --------------------------
// Strings of our menu.
// This is done to store the strings in in the program flash.
// If given like this: "some string", the strings would be placed in
// the RAM.


const char string_0  [] PROGMEM = "On ";
const char string_1  [] PROGMEM = "Off";
const char string_2  [] PROGMEM = "CW ";
const char string_3  [] PROGMEM = "CCW";
const char string_4  [] PROGMEM = "Stp:";
const char string_5  [] PROGMEM = "D:";
const char string_6  [] PROGMEM = "Program started.";
const char string_7  [] PROGMEM = "Program stopped.";
const char string_8  [] PROGMEM = "enabled";
const char string_9  [] PROGMEM = "disabled";

const char string_10 [] PROGMEM = "Camera";
const char string_11 [] PROGMEM = "Motor";
const char string_12 [] PROGMEM = "Program";
const char string_13 [] PROGMEM = "General";
const char string_14 [] PROGMEM = "Settings";
const char string_15 [] PROGMEM = "Version info";

const char string_16 [] PROGMEM = "Cycle length";
const char string_17 [] PROGMEM = "Focus time";
const char string_18 [] PROGMEM = "Exp. time";
const char string_19 [] PROGMEM = "Focus behav.";
const char string_20 [] PROGMEM = "Max. shots";
const char string_21 [] PROGMEM = "Post delay";
const char string_22 [] PROGMEM = "Test shot";

const char string_23 [] PROGMEM = "Motor steps ";
const char string_24 [] PROGMEM = "Direction";
const char string_25 [] PROGMEM = "Motor home";
const char string_26 [] PROGMEM = "Motor sleep";
const char string_27 [] PROGMEM = "Max steps";
const char string_28 [] PROGMEM = "Ramp";

const char string_29 [] PROGMEM = "Operat. mode";
const char string_30 [] PROGMEM = "B-Light time";
const char string_31 [] PROGMEM = "B-Light powr";
const char string_32 [] PROGMEM = "System time ";

const char string_33 [] PROGMEM = "Save settgs.";
const char string_34 [] PROGMEM = "Autosave";
const char string_35 [] PROGMEM = "Reset";

const char string_36 [] PROGMEM = "Developers";
const char string_37 [] PROGMEM = "(alphabt. o.):";
const char string_38 [] PROGMEM = "Airic Lenz,";
const char string_39 [] PROGMEM = "Alvarocalvo,";
const char string_40 [] PROGMEM = "C.A. Church,";
const char string_41 [] PROGMEM = "Marc Lane";
const char string_42 [] PROGMEM = "For questions";
const char string_43 [] PROGMEM = "have a look at";
const char string_44 [] PROGMEM = "openmoco.org  ";
const char string_45 [] PROGMEM = "";                // reserve

const char string_46 [] PROGMEM = "Press SELECT to";

const char string_47 [] PROGMEM = "";
const char string_48 [] PROGMEM = "";
const char string_49 [] PROGMEM = "";
const char string_50 [] PROGMEM = "";
const char string_51 [] PROGMEM = "";
const char string_52 [] PROGMEM = "";

const char string_53 [] PROGMEM = "do a test shot.";

const char string_54 [] PROGMEM = "";
const char string_55 [] PROGMEM = "";
const char string_56 [] PROGMEM = "";
const char string_57 [] PROGMEM = "";
const char string_58 [] PROGMEM = "";

const char string_59 [] PROGMEM = "Set home";
const char string_60 [] PROGMEM = "";

const char string_61 [] PROGMEM = "Add program ";
const char string_62 [] PROGMEM = "add a program.";

const char string_63 [] PROGMEM = "Start time";
const char string_64 [] PROGMEM = "Weekdays";
const char string_65 [] PROGMEM = "Duration";
const char string_66 [] PROGMEM = "Move home";
const char string_67 [] PROGMEM = "Status";
const char string_68 [] PROGMEM = "Delete";

const char string_69 [] PROGMEM = "";
const char string_70 [] PROGMEM = "";
const char string_71 [] PROGMEM = "";

const char string_72 [] PROGMEM = "save settings.";

const char string_73 [] PROGMEM = "Autosave settgs:";

const char string_74 [] PROGMEM = "reset settings.";
const char string_75 [] PROGMEM = "Restoring CFG..";
const char string_76 [] PROGMEM = "Restarting..";

const char string_77 [] PROGMEM = "set motor home.";

const char string_78 [] PROGMEM = "Move to home";
const char string_79 [] PROGMEM = "Moving motor to";
const char string_80 [] PROGMEM = "home. Stand by.";

const char string_81 [] PROGMEM = "Program start:";
const char string_82 [] PROGMEM = "M T W T F S S";
const char string_83 [] PROGMEM = "Duration:";
const char string_84 [] PROGMEM = "Move home @ end:";
const char string_85 [] PROGMEM = "Program status:";

const char string_86 [] PROGMEM = "delete program.";

const char string_87 [] PROGMEM = "high w. shutter";
const char string_88 [] PROGMEM = "low w. shutter";

const char string_89 [] PROGMEM = "continuous";
const char string_90 [] PROGMEM = "shoot-move-shoot";

const char string_91 [] PROGMEM = "anti-clockwise";
const char string_92 [] PROGMEM = "clockwise";

const char string_93 [] PROGMEM = "A limit switch";
const char string_94 [] PROGMEM = "was triggered!";

const char string_95 [] PROGMEM = "Max motor step";
const char string_96 [] PROGMEM = "limit reached!";

const char string_97 [] PROGMEM = "Max camera shot";
const char string_98 [] PROGMEM = "";

const char string_99 [] PROGMEM = "Post delay  ";
const char string_100[] PROGMEM = "Motor post delay:";

const char string_101[] PROGMEM = "Max speed";
const char string_102[] PROGMEM = "Max speed delay:";

const char string_103[] PROGMEM = "Min speed";
const char string_104[] PROGMEM = "Min speed delay:";

const char string_105[] PROGMEM = "Lmt-Switches";
const char string_106[] PROGMEM = "";

/*
   const char string_107[] PROGMEM = "Jog";
   const char string_108[] PROGMEM = "Motor jog:";
   const char string_109[] PROGMEM = "Up=CW  Down=CCW";
 */


// Now set up a table to refer to the strings (a simple list
// of all the strings we defined)

const char *const string_table[] PROGMEM =
{
	string_0,   string_1,   string_2,   string_3,   string_4,
	string_5,   string_6,   string_7,   string_8,   string_9,
	string_10,  string_11,  string_12,  string_13,  string_14,
	string_15,  string_16,  string_17,  string_18,  string_19,
	string_20,  string_21,  string_22,  string_23,  string_24,
	string_25,  string_26,  string_27,  string_28,  string_29,
	string_30,  string_31,  string_32,  string_33,  string_34,
	string_35,  string_36,  string_37,  string_38,  string_39,
	string_40,  string_41,  string_42,  string_43,  string_44,
	string_45,  string_46,  string_47,  string_48,  string_49,
	string_50,  string_51,  string_52,  string_53,  string_54,
	string_55,  string_56,  string_57,  string_58,  string_59,
	string_60,  string_61,  string_62,  string_63,  string_64,
	string_65,  string_66,  string_67,  string_68,  string_69,
	string_70,  string_71,  string_72,  string_73,  string_74,
	string_75,  string_76,  string_77,  string_78,  string_79,
	string_80,  string_81,  string_82,  string_83,  string_84,
	string_85,  string_86,  string_87,  string_88,  string_89,
	string_90,  string_91,  string_92,  string_93,  string_94,
	string_95,  string_96,  string_97,  string_98,  string_99,
	string_100, string_101, string_102, string_103, string_104,
	string_105, string_106  // , string_107, string_108, string_109
};

/*
   PROGMEM prog_char *string_table[] = {
    string_0,   string_1,   string_2,   string_3,   string_4,
    string_5,   string_6,   string_7,   string_8,   string_9,
    string_10,  string_11,  string_12,  string_13,  string_14,
    string_15,  string_16,  string_17,  string_18,  string_19,
    string_20,  string_21,  string_22,  string_23,  string_24,
    string_25,  string_26,  string_27,  string_28,  string_29,
    string_30,  string_31,  string_32,  string_33,  string_34,
    string_35,  string_36,  string_37,  string_38,  string_39,
    string_40,  string_41,  string_42,  string_43,  string_44,
    string_45,  string_46,  string_47,  string_48,  string_49,
    string_50,  string_51,  string_52,  string_53,  string_54,
    string_55,  string_56,  string_57,  string_58,  string_59,
    string_60,  string_61,  string_62,  string_63,  string_64,
    string_65,  string_66,  string_67,  string_68,  string_69,
    string_70,  string_71,  string_72,  string_73,  string_74,
    string_75,  string_76,  string_77,  string_78,  string_79,
    string_80,  string_81,  string_82,  string_83,  string_84,
    string_85,  string_86,  string_87,  string_88,  string_89,
    string_90,  string_91,  string_92,  string_93,  string_94,
    string_95,  string_96,  string_97,  string_98,  string_99,
    string_100, string_101, string_102, string_103, string_104,
    string_105, string_106 // , string_107, string_108, string_109
   };
 */

// UI status flags
//
// B0 = backlight on / off
// B1 = ui repaint flag
// B2 = settings autosave flag
// B3 = settings were changed flag
// B4 = 24h / 12h time (24 = LOW, 12 = HIGH)  not used yet
// B5 = long key press
// B6 = message on screen
// B7 =

byte ui_status = B11100000;


// wait time until backlight turns off in milliseconds
unsigned int backlight_wait = 10;

// backlight level in percent
byte backlight_level=100;

// a variable to remeber when a message started
unsigned long message_start_time;

// a variable to remeber when a message started
byte message_duration;

// --------------------------
// our Real time clock object
RTC_DS1307 RTC;
// and the current time of the system
DateTime time;







// ===================================================================================
// Arduino Setup Procedure
// ===================================================================================
void setup()
{

	//Serial.begin(9600);

	pinMode(MOTOR_DIR_PIN, OUTPUT);
	pinMode(MOTOR_STEP_PIN, OUTPUT);
	pinMode(MOTOR_SLEEP_PIN, OUTPUT);

	pinMode(CAMERA_PIN, OUTPUT);
	pinMode(FOCUS_PIN, OUTPUT);

	pinMode(LCD_BACKLIGHT_PIN, OUTPUT);

	// set motor to sleep
	digitalWrite(MOTOR_SLEEP_PIN, LOW);


	// init the LCD display
	// set up the LCD's number of columns and rows:
	lcd.begin(16, 2);
	lcd.clear();


	// did we previously save settings to eeprom?
	// is config saved and has the config has the correct version?
	if ((is_eeprom_saved()) &&
		(is_OK_eeprom_version()))
	{
		load_config();
	}
	else
	{
		write_config();
		write_eeprom_version();
	}


	// enable backlight
	setBacklightLevel();


	byte scroll_up[8] =
	{
		B00100,
		B01110,
		B11111,
		B00100,
		B00100,
		B00000,
		B00000,
		B00000
	};

	byte scroll_down[8] =
	{
		B00000,
		B00000,
		B00000,
		B00100,
		B00100,
		B11111,
		B01110,
		B00100
	};


	// create the special chars we need for the UI
	lcd.createChar(0, scroll_up);
	lcd.createChar(1, scroll_down);

	/*
	   Serial.println();
	   Serial.print(freeMemory());
	   Serial.println(" byte free.");
	 */


	// welcome screen
	lcd.setCursor(3, 0);
	lcd.print("miniEngine");
	lcd.setCursor(6, 1);
	lcd.print("v");
	lcd.print(VERSION);
	lcd.print(".");
	lcd.print(SUBVERSION);

	delay(1500);


	// RTC Stuff
	Wire.begin();
	RTC.begin();

}
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
void loop()
{

	// do the screen stuff
	do_screen();

	// programm is running
	if (action_status & B00001000)
	{

		// =================================================
		// C O N T I N U O U S   m o d e
		// =================================================
		if (action_status & B10000000)
		{

			// do some continuous steps
			doMotorContinuous();

			// if it is time or the "start a new cycle immediately" flag is set
			if ((action_status & B00100000) ||
			((program_start_time + ((unsigned long) cycle_length * 500UL * (unsigned long) camera_shoot_count)) <= millis()))
			{

				// if not exposing right now and not in camera post delay (makes this sense in continuous??)
				if (!(action_status & B01000000) &&
				    !(action_status & B00010000) &&
				    !(action_status & B00000100))
				{

					// do some continuous steps
					doMotorContinuous();

					// should we do focussing?
					if (camera_focus_time > 0)
					{
						camera_focus();
					}
					else
					{
						// shoot camera
						camera_shoot();
					}

				}

				// do some continuous steps
				doMotorContinuous();

				// delete the start immediately flag if set
				if (action_status & B00100000)
				{
					// delete the start immediately flag
					bitClear(action_status, 5);      // B11011111
				}
			}

			// do some continuous steps
			doMotorContinuous();


			// is camera focussing right now?
			if (action_status &  B01000000)
			{
				// did we focus the time we wanted to focus?
				if((action_start_time + (unsigned long) camera_focus_time) <= millis())
				{
					// stop focussing (this function automatically starts the exposure)
					camera_stop_focus();
				}
			}

			// do some continuous steps
			doMotorContinuous();

			// is camera exposing right now?
			if (action_status &  B00010000)
			{
				// did we exposed the time we wanted to expose?
				if((action_start_time + (unsigned long)camera_exp_time) <= millis())
				{
					// stop shooting
					camera_stop_shoot();
				}
			}

			// do some continuous steps
			doMotorContinuous();

			// now check the limit switches if we need to stop the program
			// this function is called as late as possible after the key reading because
			// analogRead needs some pre delay time to deliver accurate measurements...
			check_limit_switches();

		}

		// =================================================
		// S H O O T - M O V E - S H O O T   m o d e
		// =================================================
		else {

			// if it is time or the "start a new cycle immediately" flag is set
			if ((action_status & B00100000) ||
				((program_start_time + ((unsigned long) cycle_length * 500UL * (unsigned long) camera_shoot_count)) <= millis()))
			{
				// if not focussing or exposing right now and not in camera or motor post delay
				if (!(action_status & B01000000) &&
					!(action_status & B00010000) &&
					!(action_status & B00000100) &&
					!(action_status & B00000001) )
				{
					// should we do focussing?
					if (camera_focus_time > 0)
					{
						camera_focus();
					}
					else
					{
						// shoot camera
						camera_shoot();
					}
				}


				// delete the start immediately flag if set
				if (action_status & B00100000)
				{
					// toggle the start immediately flag to off
					bitClear(action_status, 5);
				}
			}


			// is camera focussing right now?
			if (action_status &  B01000000)
			{
				// did we focus the time we wanted to focus?
				if((action_start_time + (unsigned long) camera_focus_time) <= millis())
				{
					// stop focussing (this function automatically starts the exposure)
					camera_stop_focus();
				}
			}


			// is camera exposing right now?
			if (action_status &  B00010000)
			{
				// did we exposed the time we wanted to expose?
				if((action_start_time + camera_exp_time) <= millis())
				{
					// stop shooting
					camera_stop_shoot();
				}
			}


			// post exposure delay
			if (action_status & B00000100)
			{
				// did we exposed the time we wanted to expose?
				if((action_start_time + (unsigned long) camera_exp_time + (unsigned long) camera_exp_post) <= millis())
				{
					camera_stop_post();
				}
			}


			// time for the engines
			if (action_status & B00000010)
			{
				// do the blocking motor phase with error check
				doMotorPhase(true);

				motor_stop();

				// now check the limit switches if we need to stop the program
				// this function is called after the blocking motor phase because
				// analogRead needs some pre delay time to deliver accurate
				// measurements...
				check_limit_switches();

			}


			// motor post delay
			if (action_status & B00000001)
			{
				// did we waited the time we wanted to wait?
				if((action_start_time + (unsigned long) motor_post) <= millis())
				{
					// clear the waintg flag...
					bitClear(action_status, 0);      // B11111110
				}
			}

		}   // operation mode


		// if the programm is running and we are in contiuous mode
		continuous_check();

	}   // program is running

	// read the time from the RTC (valid for the next loop)
	time = RTC.now();

	// if the programm is running and we are in contiuous mode
	continuous_check();

	// the function that checks if we need to start or stop a program
	check_programs();

	// if the programm is running and we are in contiuous mode
	continuous_check();

	// check if there are programs that will be triggered in the future
	// this is done for being able to display this information ("smart P")
	check_programFuture();

}

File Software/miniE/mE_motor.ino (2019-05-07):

/*

    See www.openmoco.org for more information

    2015 Airic Lenz

    The 1st version of this code, dealing with core functionalities,
    was heavily inspired by the OpenMoCo Engine by C.A. Church
    and is basically based on it. Thank you for your great work!

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
 */

// milliseconds needed to let the motor settle and break after
// action (before sleep is activated)
#define    motor_break_delay 6


// count the number of pulses
unsigned long step_count = 0;

// delta between min speed delay and max speed delay
unsigned long delay_delta;

// the ramp that is used (after corrections)
unsigned long used_motor_ramp;

// constinuous mode variables
float steps_per_milli;

// the number of steps we need to to for the next continuous phase
unsigned long steps_to_do;

// the time
unsigned long now;

// counter fot all continuous steps done
unsigned long continuous_steps_done;

// when did we check the limit switches the last time?
unsigned long limit_switch_last_time;

// tollgle flagg for measuring the limit switches and keys - but not at the samt time
byte analog_measure_toggle;


// ===================================================================================
void motor_start()
{

	// start the motor phase if we have motor_steps defined
	if (motor_steps > 0)
	{

		prepare_motor_values();

		// open the slot for the motor
		action_status |= B00000010;
	}
}

// ===================================================================================
void motor_stop()
{

	// close the time slot for the motor
	bitClear(action_status, 1);

	// if we want a motor post delay, activate is now
	if (motor_post > 0)
	{

		// set the corresponding flag
		action_status |= B00000001;

		// remember the time we started
		action_start_time = millis();
	}

}



// ===================================================================================
void doMotorContinuous()
{

	now = millis();

	//               |  time total since start * s_p_m = theoret. steps total |
	steps_to_do =    ( (float) (now - program_start_time) * steps_per_milli   ) - continuous_steps_done;


	// check if our next move will reach the max step limit
	if ( (motor_steps_max != 0) &&
	     ((abs((unsigned long) home_steps) + (unsigned long) steps_to_do) >= motor_steps_max))
	{

		// stop the program
		stop_program();

		// print a message: "Max motor step limit reached!";
		print_message(95, 96, 3);

		return;
	}


	// do all the steps we need to do
	for (long i=0; i < steps_to_do; i++)
	{

		// Move stepper one pulse using delay just calculated
		digitalWrite(MOTOR_STEP_PIN, HIGH);
		delayMicroseconds(5);
		digitalWrite(MOTOR_STEP_PIN, LOW);

		//delayMicroseconds(200);
		delayMicroseconds(motor_step_delay_min);

		continuous_steps_done++;
	}

	// add the steps to the home counter
	// depends on the current motor direction
	if (motor_status & B00001000)
	{
		home_steps -= (long) steps_to_do;
	}
	else
	{
		home_steps += (long) steps_to_do;
	}

}




// ===================================================================================
boolean doMotorPhase(boolean check_for_errors)
{

	step_count = 0;

	if (check_for_errors)
	{

		// check if our next move will reach the max step limit
		if ( (motor_steps_max != 0) &&
		     ((abs(home_steps) + motor_steps) > motor_steps_max))
		{

			// stop the program
			stop_program();

			// print a message: "Max motor step limit reached!";
			print_message(95, 96, 3);

			return false;
		}
	}

	// wake up the engine
	digitalWrite(MOTOR_SLEEP_PIN, HIGH);


	// while there are still steps to do...
	while (step_count < motor_steps)
	{

		now = millis();


		// do some analog readings
		if (limit_switch_last_time + 50UL <= now)
		{

			int val;

			if      (analog_measure_toggle == 0) val = analogRead(LIMIT_SWITCH_PIN_1);
			else if (analog_measure_toggle == 1) val = analogRead(LIMIT_SWITCH_PIN_2);
			else val = analogRead(LCD_KEY_PIN);

			if (analog_measure_toggle == 2)
			{

				// if we have a pressed SELECT key
				if ((val > key_3_val) && (val < key_4_val))
				{
					// stop the program
					stop_program();
					display_home();
					delay (250);
					return true;
				}

				// if we should check for error and
				// if the limit switches are enabled
			}
			else if ((check_for_errors) &&
			           (motor_status & B01000000))
			{

				// if we have a triggered limit switch
				if (val >= 1000) {
					limit_switch_event();
					return false;
				}
			}

			// toggle the toggle flag to the next position (3 positions)
			if (analog_measure_toggle == 2) analog_measure_toggle = 0;
			else analog_measure_toggle++;

			// remember the last time we measured
			limit_switch_last_time = now;
		}


		// determine the ramp delay for the current step
		unsigned long step_delay = calculate_ramp_delay();


		// Move stepper one pulse using the delay just calculated
		digitalWrite(MOTOR_STEP_PIN, HIGH);
		delayMicroseconds(5);
		digitalWrite(MOTOR_STEP_PIN, LOW);
		delayMicroseconds(step_delay);
		step_count++;


		// add the step to the home variables
		// depending on the motor direction

		if (motor_status & B00001000) home_steps--;
		else home_steps++;

	}



	// wait a little time to let the motor settle and break
	delay (motor_break_delay);

	// bring the engine back to sleep if desired
	if (motor_status & B10000000)
	{
		digitalWrite(MOTOR_SLEEP_PIN, LOW);
	}

	return true;

}


// ===================================================================================
unsigned long calculate_ramp_delay()
{

	unsigned long res;
	float x_scale;

	// acceleration phase
	if (step_count < used_motor_ramp)
	{

		// x scale represents the position in the current speed-phase between 0 (beginning) and 1 (end)
		x_scale = (float) step_count / (float) used_motor_ramp;
	}

	// reached deceleration phase
	else if (step_count > (motor_steps - used_motor_ramp))
	{

		// x scale represents the position in the current speed-phase between 0 (beginning) and 1 (end)
		x_scale = (float) (motor_steps - step_count) / (float) used_motor_ramp;

	}

	// reached max speed phase
	else
	{

		// wait a little bit because here should be a calculation which requires some time
		// (each calc required a different amount);
		switch(MOTOR_RAMP_TYPE)
		{
			case RAMPING_LINEAR:    delayMicroseconds(50); break;
			case RAMPING_ATANGENS:  delayMicroseconds(200); break;
			case RAMPING_SINUS:     delayMicroseconds(200); break;
		}

		// now return the result
		return motor_step_delay_min;
	}

	switch(MOTOR_RAMP_TYPE)
	{
		case RAMPING_LINEAR:
			res = x_scale * delay_delta;
			break;
		case RAMPING_ATANGENS:
			res = (atan(15.0 * x_scale) / 1.51) * delay_delta;      // more steep curve
			break;
		case RAMPING_SINUS:
			res = (((cos(PI * (x_scale - 1))) / 2) + 0.5) * delay_delta;
			break;
	}


	if (motor_step_delay_min > (motor_step_delay_max - res))
	{
		return motor_step_delay_min;
	}
	else
	{
		return motor_step_delay_max - res;
	}

}
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

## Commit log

2015-02-23 initial commit to GitHub
    [miniE_arduino_shield_v1-3.brd, miniE_arduino_shield_v1-3.sch]
2015-02-23 corrected version and release year
    [mE_camera.ino, mE_core.ino, mE_eeprom.ino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]
2015-03-10 added documentation for acrylic enclosure
